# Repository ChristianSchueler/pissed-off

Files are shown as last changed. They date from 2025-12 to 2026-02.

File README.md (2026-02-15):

# Le Petit Julien: Pissed Off - Interactive Mechatronic Cocktail Art Installation

Interactive exhibit of "Petit Julien" ("Manneken Piss"), urinating drinks.

> This little bastard takes care of some some yellow-screwdriver revenge for 
> you. Admit it: you’ve already dreamt of that at least once.
> [Roboexotica 2025](https://roboexotica.at/?exhibition2025)

Roboexotica 2025: [Photos of exhibition](https://www.esel.at/de/album/roboexotica-2025--031s2bxzYJqxJ13hXJkv2q)

The statue is made of plaster, sized 2/3 of the original. It features a liquid
pumping system, a digital scale and a coin acceptor to donate coins. It is controlled by a ESP-32 and C code.

## Technical brief
```
Plaster cast in a 1.5 mm PLA 3D-printed mold, 6 mm plywood box, 8 mm aluminum tube,
2.5 mm silicone rubber hose, ESP32-S3 microcontroller, 492 lines of C code, LM2596
DC-DC voltage converter, 1 kg load cell with strain gauge, HX711 24-bit A/D converter,
DG600F coin acceptor, 12 V peristaltic pump with controller board, 1-channel relay,
PLA 3D-printed weighing pan, 10 L water canister.
```

See /esp-32-s3 subfolder for microcontroller source code.

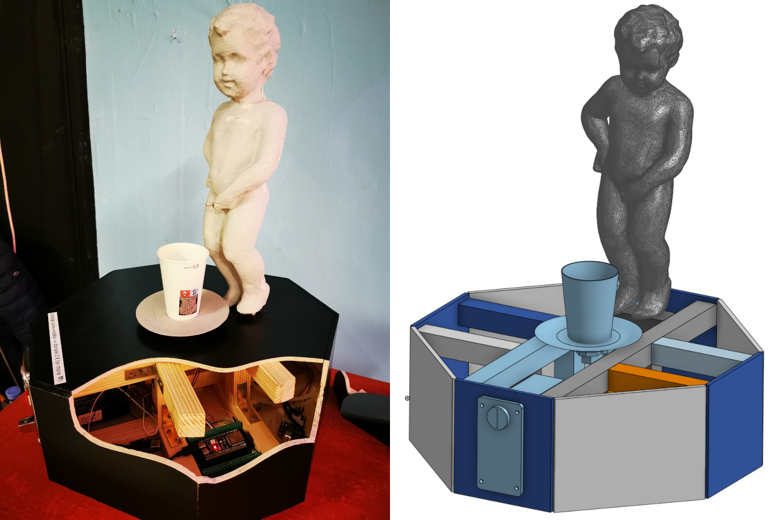
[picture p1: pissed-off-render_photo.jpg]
pissed off project on display during exhibition: statue on wooden box.


# Pissed Off ESP32-S3 Code

This ESP-32 code controls the following hardware:

- load cell
- peristaltic pump
- coin acceptor

## Loop - wait for donation and cup, then dispense a cocktail; repeat

- count coins, measure load
- INSERT_COIN: when coins reach price for a defined duration AND load = empty cup:
  - set drink size based on donation (hint: does only work if donating first, then placing cup)
  - switch on peristaltic pump
  - state -> DISPENSING
- DISPENSING: 
  - measure dispensed
  - when load = full cup OR timeout (empty supply) OR load = 0 (someone took cup or cup fell):
    - switch off peristaltic pump
    - state -> TAKE_CUP or INSERT_COIN if someone took the cup
- TAKE_CUP: when load = empty:
    - reset coins (only here when full cocktail has been dispensed, otherwise credits remain valid)
    - tare
    - state -> INSERT_COIN

## Connect to ESP32

powershell:
```
usbipd list
usbipd attach --wsl --auto-attach --busid 10-2
```

wsl:
```
ls /dev
```
look for ttyACM0 (on my machine) and set in esp-idf config

## Ideas and Todo

- measuring the weight when placing a cup takes place only once. this might lead
  to wrong weight when users move the cup around and press.
- nive to have: count all donated coins across the session and store overall coint coin, preferably by day + have a way to output the amount
  - could use NVS to store an int 32 per day, marked by key name, e.g. key = "coins_2025-11-23", value = 4000 meaning EUR 40,-
  - would have to use NVS iterator to get all coins donated OR simply try to get keys for certain dates
  
# 3D CAD

Files in STL format sit in /3d_cad and have been created in OnShape. The mold is split in half and then again split in 4 parts for printing.

# Updates

* 15.02.2026: fixed "relay not working". reason: relay power 3.3 V too low. solution: raised overall voltage from 3.3 V to 5.0 V via the DC-DC converter. switched esp-32 power connector from 3.3 V pin to 5V pin.

(c) 2025, Christian Schüler, hello@christianschueler.at

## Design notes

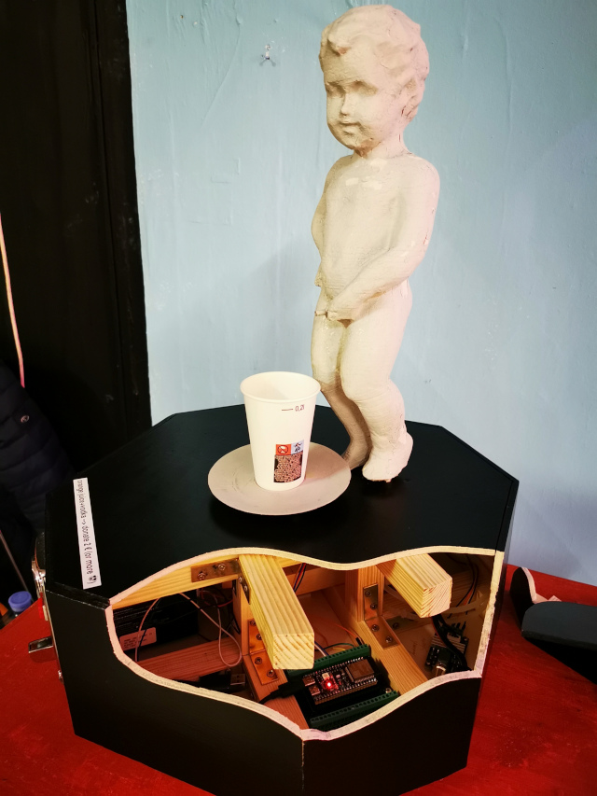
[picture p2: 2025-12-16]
pissed-off-2025_640x853.jpg

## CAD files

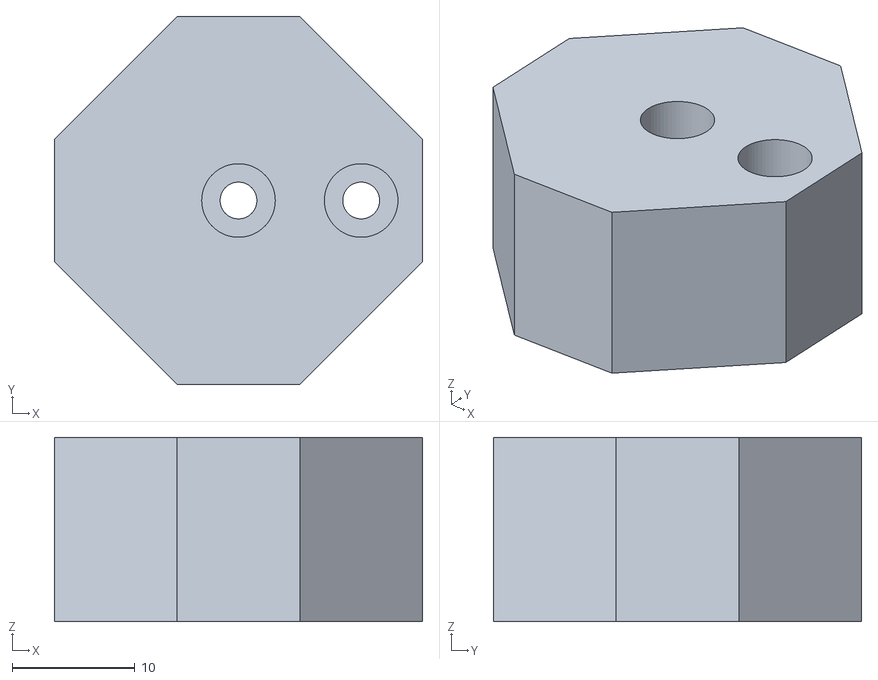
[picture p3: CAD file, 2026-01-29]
3d_cad/pissed off - load cell connector.stl
30.0 x 30.0 x 15.0

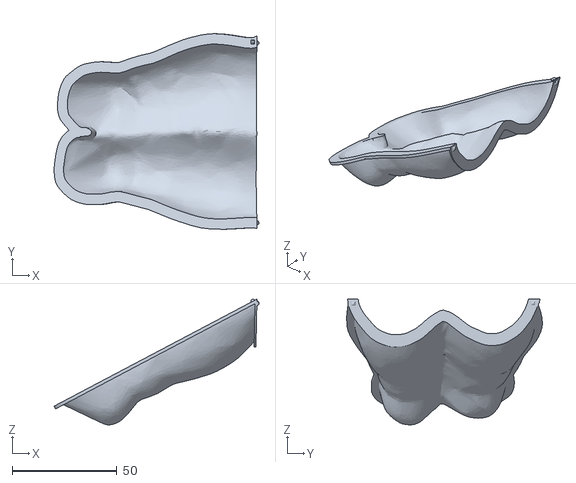
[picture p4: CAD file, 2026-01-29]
3d_cad/boy-statue-back-hull-1.stl
98.0 x 93.5 x 60.2

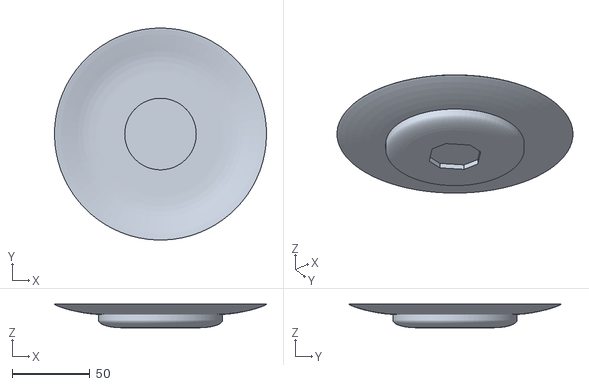
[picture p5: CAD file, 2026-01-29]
3d_cad/pissed off - cup holder.stl
136.3 x 136.3 x 15.1

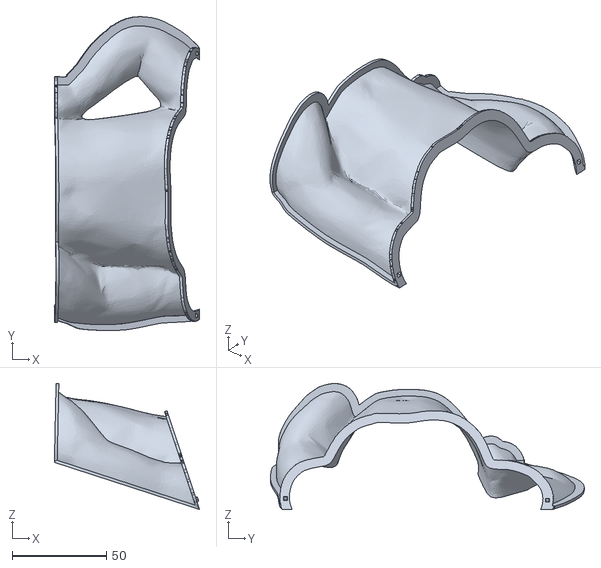
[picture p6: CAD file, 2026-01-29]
3d_cad/boy-statue-front-hull-3.stl
77.1 x 166.6 x 66.9

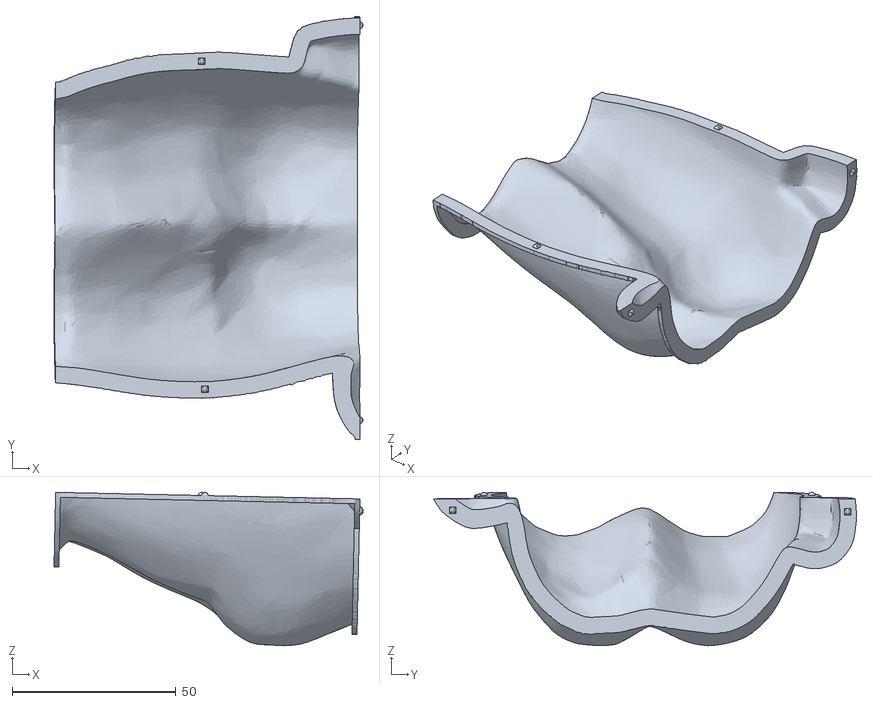
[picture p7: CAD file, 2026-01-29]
3d_cad/boy-statue-back-hull-2.stl
94.3 x 129.2 x 46.9

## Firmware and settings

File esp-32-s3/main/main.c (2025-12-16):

// (c) 2025, Christian Schüler, hello@christianschueler.at

#include <stdio.h>
#include "freertos/FreeRTOS.h"
#include "freertos/task.h"
#include <driver/gpio.h>
#include "driver/uart.h"
#include "peristaltic-pump.h"
#include "coin-acceptor.h"
#include "load-cell.h"
#include <esp_timer.h>

#define VERSION 1.0
//#define DEBUG_PRINTF 1

enum State {
  INSERT_COIN,          // donate coins
  DISPENSING,           // dispense drink
  TAKE_CUP              // waiting to take cup
};

#define MAIN_LOOP_DELAY_MS 100                // how much we intentionally slow down the main loop -> 100 ms by default
#define COCKTAIL_MIN_DONATION_SMALL_CENTS 200 // donate at least eur 2 for small cup
#define COCKTAIL_MIN_DONATION_LARGE_CENTS 300 // donate at least eur 3 for larger cup
#define COCKTAIL_SIZE_SMALL_ML 100            // small drink is 10 ml
#define COCKTAIL_SIZE_LARGE_ML 180            // large drink is 18 ml, as in original recipe
#define CUP_WEIGHT_MIN_GRAMS 3                // minimum empty cup weight, used to identify placement of a cup
#define CUP_WEIGHT_MAX_GRAMS 1000             // maximum empty cup weight -> 1000 g: be sure to accept EVERY cup
#define DISPENSING_TIMEOUT_MS 1500*60         // after dispensing time out we stop; most probably empty supply
#define MIN_FILL_DURATION_MS 1000             // how long we fill the cup at least, even if someone removed the cup (necessary to ignore load scale measures bouncing)
#define MIN_DISPENSING_DELAY_MS 1000*2        // start 2 s after (!) placing the cup to make sure shaky hands do get splashed (trust me with this one)

enum State state = INSERT_COIN;               // simple state based application with 3 states

float initial_weight_grams;                   // remember weight when starting to fill the cup. most probably very small
int targetDrinkSize_ml;                       // either small or large amount, will be set in INSERT_COIN state

// computation of data types for times: microsecs: 86.400.000.000 per 24 hours
// long int: max.: 2.147.483.647 -> overflow after about 1h 40s! 
// -> we need 64 bit, i.e. int64_t

uint64_t dispensing_started_time_ms;          // when we started to dispense; used for timeout
int64_t cup_placed_time_ms = -1;              // when we placed the cup; used to wait a bit until the hands are away

void app_main(void)
{
    printf("Pissed Off - Mechatronic Interactive Cocktail Machine, (c) 2025 Christian Schüler, hello@christianschueler.at\n");
    printf("Version: %1.1f\n", VERSION);

    printf("application: starting initialization...\n");
    peristaltic_pump_init();    // first, such that even if everythink else fails, the pump gets stopped
    coin_acceptor_init();
    load_cell_init();

    printf("application: initialized.\n");

    printf("starting main loop, tick duration: %d ms.\n", MAIN_LOOP_DELAY_MS);
    printf("pissed off: insert coin\n");

    while (1) {
        peristaltic_pump_loop();
        coin_acceptor_loop();
        load_cell_loop();

        // keep track of donation and weight
        float weight = load_cell_get_last_load_grams();
        int coins = coin_acceptor_get_amount_cents();

        #ifdef DEBUG_PRINTF
        printf("DEBUG - state: %d\n", state);
        #endif

        switch (state) {
          // -------------------------------------------------------------------------------------------------------------------------------------------
          case INSERT_COIN:
            int cup_placed = (weight >= CUP_WEIGHT_MIN_GRAMS && weight <= CUP_WEIGHT_MAX_GRAMS);    // true when cup is present

            // remember when we placed the cup (or -1 when no cup present)
            if (cup_placed) {   // if cup has been placed just now
              if (cup_placed_time_ms < 0) {
                cup_placed_time_ms = esp_timer_get_time()/1000;
                printf("pissed off: empty cup has been placed\n");
                printf("pissed off: empty cup weight: %1.1f g\n", weight);
              }
            }
            else {     // if cup has been lifted just now
              if (cup_placed_time_ms > 0) {
                cup_placed_time_ms = -1;
                printf("pissed off: empty cup has been taken\n");
              }
            }

            // compute how long the cup has been present (or -1 when not present)
            long int duration_cup_present_ms;
            if (cup_placed && cup_placed_time_ms >= 0) {
              duration_cup_present_ms = (esp_timer_get_time() - cup_placed_time_ms*1000)/1000;
              #ifdef DEBUG_PRINTF
              printf("pissed off: cup present duration: %ld ms\n", duration_cup_present_ms);
              #endif
            }
            else duration_cup_present_ms = -1;

            // coins donated, cup present for long enough? -> go!
            if (coins >= COCKTAIL_MIN_DONATION_SMALL_CENTS && 
                cup_placed &&
                duration_cup_present_ms >= MIN_DISPENSING_DELAY_MS) {   // if enough donation and cup is present and at least some time has passed since placing the cup
                  printf("pissed off: coins donated: %d\n", coins);
                  
                  // decide drink size depending on donation
                  if (coins >= COCKTAIL_MIN_DONATION_LARGE_CENTS) targetDrinkSize_ml = COCKTAIL_SIZE_LARGE_ML;
                  else targetDrinkSize_ml = COCKTAIL_SIZE_SMALL_ML;

                  printf("pissed off: drink size selected: %d ml\n", targetDrinkSize_ml);
                  printf("pissed off: coins donated and cup placed -> dispensing\n");

                  initial_weight_grams = weight;
                  dispensing_started_time_ms = esp_timer_get_time()/1000;
                  set_peristaltic_pump_on();
                  
                  state = DISPENSING;
                }
            break;

          // -------------------------------------------------------------------------------------------------------------------------------------------
          case DISPENSING:
            int drink_dispensed_ml = weight - initial_weight_grams;    // assuming ml == grams
            uint64_t duration_ms = (esp_timer_get_time() - dispensing_started_time_ms*1000)/1000;
            int tookCup = (weight < CUP_WEIGHT_MIN_GRAMS && duration_ms >= MIN_FILL_DURATION_MS);

            #ifdef DEBUG_PRINTF
            printf("DEBUG - drink_dispensed_ml: %d\n", drink_dispensed_ml);
            printf("DEBUG - duration_ms: %lld\n", duration_ms);
            #endif

            // if we either have reached drink size or timeout -> stop
            if (drink_dispensed_ml >= targetDrinkSize_ml || duration_ms > DISPENSING_TIMEOUT_MS) {    // cup is filled or timeout (e.g. ran out of booze)
              if (duration_ms > DISPENSING_TIMEOUT_MS) printf("pissed off: ERROR ran out of supply\n");
              else printf("pissed off: cup filled -> take cup\n");
              set_peristaltic_pump_off();
              state = TAKE_CUP;
            }
            else if (tookCup) {   // someone removed the cup mid-dispensing ot it "fell" down -> stop!
              printf("pissed off: ERROR cup removed -> insert coin\n");
              set_peristaltic_pump_off();
              cup_placed_time_ms = -1;
              state = INSERT_COIN;
            }
            break;

          // -------------------------------------------------------------------------------------------------------------------------------------------
          case TAKE_CUP:
            if (weight < CUP_WEIGHT_MIN_GRAMS) {
              printf("pissed off: cup taken -> insert coin\n");
              coin_acceptor_reset_amount();
              cup_placed_time_ms = -1;
              load_cell_tare();                       // reset load cell every time to account for drift
              state = INSERT_COIN;
            }
            break;
        }

        vTaskDelay(MAIN_LOOP_DELAY_MS / portTICK_PERIOD_MS);
    }
}

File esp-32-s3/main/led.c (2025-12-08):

// /*
//  * SPDX-FileCopyrightText: 2023-2024 Espressif Systems (Shanghai) CO LTD
//  *
//  * SPDX-License-Identifier: Unlicense OR CC0-1.0
//  */
// #include <stdio.h>
// #include "freertos/FreeRTOS.h"
// #include "freertos/task.h"
// #include "led_strip.h"
// #include "esp_log.h"
// #include "esp_err.h"

// // Set to 1 to use DMA for driving the LED strip, 0 otherwise
// // Please note the RMT DMA feature is only available on chips e.g. ESP32-S3/P4
// #define LED_STRIP_USE_DMA  0

// #if LED_STRIP_USE_DMA
// // Numbers of the LED in the strip
// #define LED_STRIP_LED_COUNT 256
// #define LED_STRIP_MEMORY_BLOCK_WORDS 1024 // this determines the DMA block size
// #else
// // Numbers of the LED in the strip
// #define LED_STRIP_LED_COUNT 24
// #define LED_STRIP_MEMORY_BLOCK_WORDS 0 // let the driver choose a proper memory block size automatically
// #endif // LED_STRIP_USE_DMA

// // GPIO assignment
// #define LED_STRIP_GPIO_PIN  2

// // 10MHz resolution, 1 tick = 0.1us (led strip needs a high resolution)
// #define LED_STRIP_RMT_RES_HZ  (10 * 1000 * 1000)

// static const char *TAG = "example";

// led_strip_handle_t configure_led(void)
// {
//     // LED strip general initialization, according to your led board design
//     led_strip_config_t strip_config = {
//         .strip_gpio_num = LED_STRIP_GPIO_PIN, // The GPIO that connected to the LED strip's data line
//         .max_leds = LED_STRIP_LED_COUNT,      // The number of LEDs in the strip,
//         .led_model = LED_MODEL_WS2812,        // LED strip model
//         .color_component_format = LED_STRIP_COLOR_COMPONENT_FMT_GRB, // The color order of the strip: GRB
//         .flags = {
//             .invert_out = false, // don't invert the output signal
//         }
//     };

//     // LED strip backend configuration: RMT
//     led_strip_rmt_config_t rmt_config = {
//         .clk_src = RMT_CLK_SRC_DEFAULT,        // different clock source can lead to different power consumption
//         .resolution_hz = LED_STRIP_RMT_RES_HZ, // RMT counter clock frequency
//         .mem_block_symbols = LED_STRIP_MEMORY_BLOCK_WORDS, // the memory block size used by the RMT channel
//         .flags = {
//             .with_dma = LED_STRIP_USE_DMA,     // Using DMA can improve performance when driving more LEDs
//         }
//     };

//     // LED Strip object handle
//     led_strip_handle_t led_strip;
//     ESP_ERROR_CHECK(led_strip_new_rmt_device(&strip_config, &rmt_config, &led_strip));
//     ESP_LOGI(TAG, "Created LED strip object with RMT backend");
//     return led_strip;
// }

// void app_main(void)
// {
//     led_strip_handle_t led_strip = configure_led();
//     bool led_on_off = false;

//     ESP_LOGI(TAG, "Start blinking LED strip");
//     while (1) {
//         if (led_on_off) {
//             /* Set the LED pixel using RGB from 0 (0%) to 255 (100%) for each color */
//             for (int i = 0; i < LED_STRIP_LED_COUNT; i++) {
//                 ESP_ERROR_CHECK(led_strip_set_pixel(led_strip, i, 5, 5, 5));
//             }
//             /* Refresh the strip to send data */
//             ESP_ERROR_CHECK(led_strip_refresh(led_strip));
//             ESP_LOGI(TAG, "LED ON!");
//         } else {
//             /* Set all LED off to clear all pixels */
//             ESP_ERROR_CHECK(led_strip_clear(led_strip));
//             ESP_LOGI(TAG, "LED OFF!");
//         }

//         led_on_off = !led_on_off;
//         vTaskDelay(pdMS_TO_TICKS(500));
//     }
// }

// ----

// #define BLINK_GPIO 0

// /// LED strip common configuration
// led_strip_config_t strip_config = {
//     .strip_gpio_num = BLINK_GPIO,  // The GPIO that connected to the LED strip's data line
//     .max_leds = 1,                 // The number of LEDs in the strip,
//     .led_model = LED_MODEL_WS2812, // LED strip model, it determines the bit timing
//     .color_component_format = LED_STRIP_COLOR_COMPONENT_FMT_GRB, // The color component format is G-R-B
//     .flags = {
//         .invert_out = false, // don't invert the output signal
//     }
// };

// /// RMT backend specific configuration
// led_strip_rmt_config_t rmt_config = {
//     .clk_src = RMT_CLK_SRC_DEFAULT,    // different clock source can lead to different power consumption
//     .resolution_hz = 10 * 1000 * 1000, // RMT counter clock frequency: 10MHz
//     .mem_block_symbols = 64,           // the memory size of each RMT channel, in words (4 bytes)
//     .flags = {
//         .with_dma = false, // DMA feature is available on chips like ESP32-S3/P4
//     }
// };

// /// Create the LED strip object
// led_strip_handle_t led_strip = NULL;
// ESP_ERROR_CHECK(led_strip_new_rmt_device(&strip_config, &rmt_config, &led_strip));

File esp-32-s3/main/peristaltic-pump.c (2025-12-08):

// (c) 2025, Christian Schüler, hello@christianschueler.at

#include <driver/gpio.h>
#include "peristaltic-pump.h"
#include "coin-acceptor.h"

#define PERISTALTIC_PUMP_PIN GPIO_NUM_1

// how many milliliters of drinks we dispensed
float peristaltic_pump_amount_dispensed_ml;

gpio_config_t io_conf = {
    .pin_bit_mask = (1ULL << PERISTALTIC_PUMP_PIN),      // Select GPIO 1
    .mode = GPIO_MODE_OUTPUT,                // Set as output
    .pull_up_en = GPIO_PULLUP_DISABLE,       // Disable pull-up
    .pull_down_en = GPIO_PULLDOWN_DISABLE,   // Disable pull-down
    .intr_type = GPIO_INTR_DISABLE           // Disable interrupts
};

int peristaltic_pump_onoff = 0;

void peristaltic_pump_init() {
    
    printf("peristaltic pump: initializing...\n");
    gpio_config(&io_conf);
    gpio_set_level(PERISTALTIC_PUMP_PIN, 0);

    peristaltic_pump_amount_dispensed_ml = 0;
    printf("peristaltic pump: initialized.\n");
}

void peristaltic_pump_loop() {
    
    // if (coin_acceptor_get_amount_cents() >= 300) {
    //     printf("Paid.\n");
    //     onoff = !onoff;
    //     printf("on/off: %d\n", onoff);
    //     gpio_set_level(PERISTALTIC_PUMP_PIN, onoff);    // toggle GPIO pin high / low
    //     coin_acceptor_reset_amount();
    // }

    // //printf("[%d] Hello world!\n", i);
    // //int onoff = i % 2;
    // //printf("on/off: %d\n", onoff);
    // //gpio_set_level(PUMP_PIN, onoff);    // toggle GPIO pin high / low
    // //i++;

    // // int length = 0;
    // // ESP_ERROR_CHECK(uart_get_buffered_data_len(COIN_ACCEPTOR_UART_NUM, (size_t*)&length));
    // // if (length > 0) {
    // //     length = uart_read_bytes(COIN_ACCEPTOR_UART_NUM, data, length, 100);
    // //     printf("%d bytes received: 0x ", length);
    // //     for (int i=0; i<length; i++) { 
    // //         printf("%x", data[i]); 
    // //         if (i < length-1) printf(" ");
    // //     }
    // //     printf("\n");
    // // }
}

void set_peristaltic_pump_on() {
    printf("peristaltic pump: on\n");
    peristaltic_pump_onoff = 1;
    gpio_set_level(PERISTALTIC_PUMP_PIN, peristaltic_pump_onoff);    // toggle GPIO pin high
}

void set_peristaltic_pump_off() {
    printf("peristaltic pump: off\n");
    peristaltic_pump_onoff = 0;
    gpio_set_level(PERISTALTIC_PUMP_PIN, peristaltic_pump_onoff);    // toggle GPIO pin high
}

bool get_peristaltic_pump_state() {
    return peristaltic_pump_onoff;
}

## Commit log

2025-11-16 coin acceptor, using UART comm., basic test working
2025-11-22 move peristaltic pump code into reparate files, add load cell scale factor and offset, add main loop to readme, several settings
2025-11-24 add led strip component and example code to control internal led
2025-12-08 add VERSION, fixe line breaks in printf
    [led.c, load-cell.c, main.c]
2025-12-08 add DEBUG_PRINTF, add some missing line breaks, fixed missing conversion from microsecs to millisecs
    [coin-acceptor.c, load-cell.c, main.c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]
2025-12-09 fix bug in load calculation formula (originally copied from some crappy but wrong lib) -> now handcrafted
    [load-cell.c]
2025-12-09 fix load cell tare to use new offset, fix data types, cup present duration now working
    [load-cell.c, main.c]
2025-12-11 longer timeout to compensate larger drinks, disable debug print, minor german typo fix
    [main.c]
2026-01-29 add link to exhibition, add link to photos, add 3d cad files
    [boy-statue-back-hull-1.stl, boy-statue-back-hull-2.stl, boy-statue-front-hull-3.stl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]
2026-02-15 change voltage to 5V, add relay manuals
